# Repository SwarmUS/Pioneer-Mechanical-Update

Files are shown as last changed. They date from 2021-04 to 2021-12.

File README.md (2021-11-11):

# Pioneer-Mechanical-Update

This repository contains the 3D model of a modified Pioneer 2-DX used by the SwarmUS project.

## Requirements
- Solidworks 2021

## Getting started

This repository contains submodule of 3D model parts. Right after cloning the project and prior to opening any assembly, run the following command:

```
git submodule update --init --recursive
```

### Repository structure

------

```
Pioneer-Mechanical-Update
├── outputs
│   ├── dxf
|   ├── pdf
│   └── STL
|   	├── external
│   	└── internal
├── external
│   └── HiveBoard-BeeBoard-Mechanical
├── internal
├── Pioneer_originalRobotBase
├── pioneer2DX.SLDASM
└── README.md
```

#### pioneer2DX.SLDASM

Main assembly of the modified pioneer. It's composed of a Pioneer 3Dx chassis (which is the same as the Pioneer 2Dx) get from *Pioneer_originalRobotBase*, of components that are external to the robot (*external*) and of components that are internal to the robot (*internal*).

In this assembly, the Realsense D435i and its support are used but an additional models were made to use a D455 instead. The D455 version is include in assembly in hidden mode. 

Note: The wheels and the front sonar array are not included in the assembly since they are not useful to the sensors and electronics layouts. 

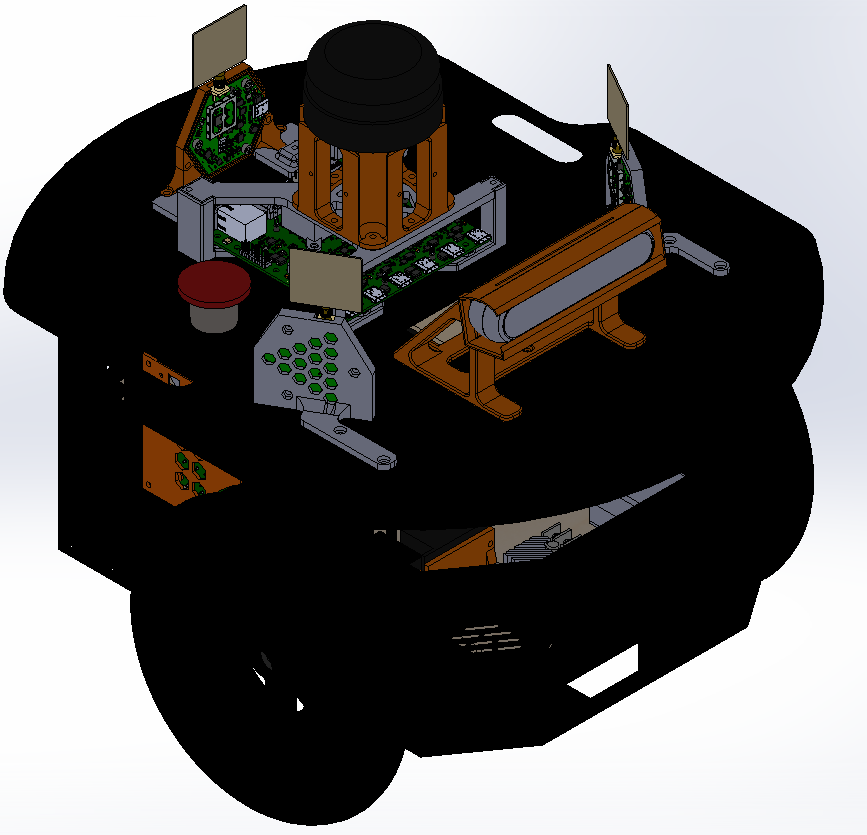
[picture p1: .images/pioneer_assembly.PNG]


### external

Contains the 3D models of the external components and their supports

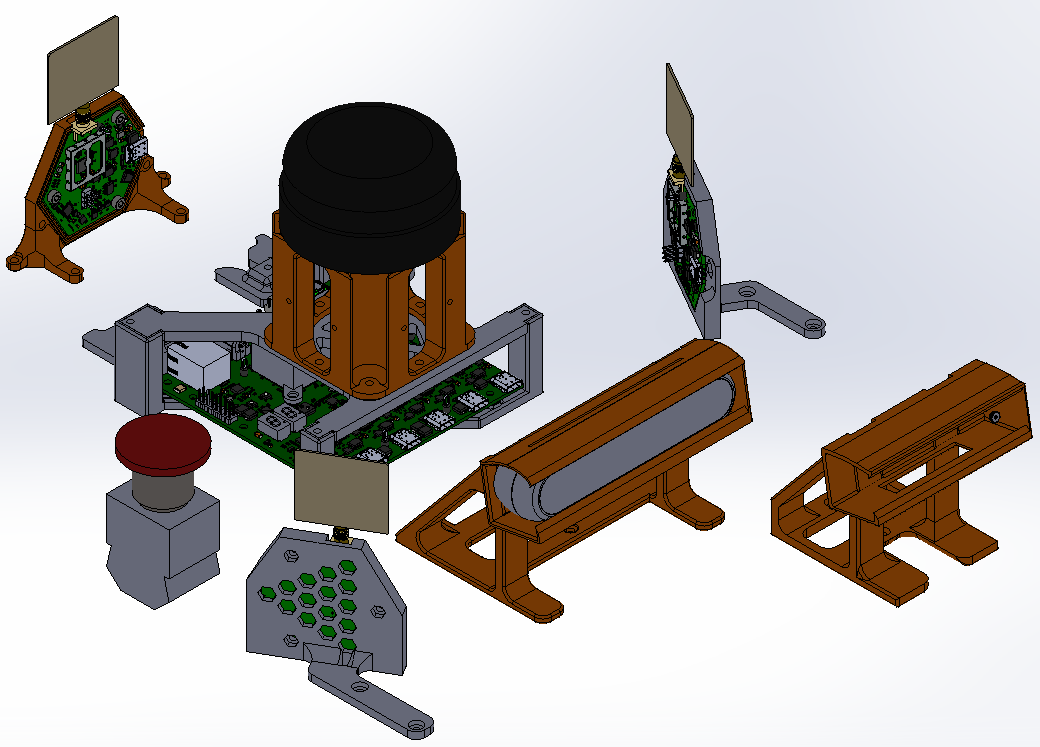
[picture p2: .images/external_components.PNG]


- **D435i**
  - **D435i_case.sldprt**: Realsense D435i protective case
  - **Intel_RealSense_Depth_Camera_D435.SLDASM**: 3D model of the camera distributed by Realsense [CAD Files (intelrealsense.com)](https://dev.intelrealsense.com/docs/cad-files)
  - **D435i_support.sldprt**: Camera stand that fits on the bolt pattern of the pioneer's top plate. The protective case is compatible with the support.
  - **D435i.SLDASM**: Assembly of the camera, its protective case and its support.
  - **protected_D435i.SLDASM**: Assembly of the camera and its protective case.
  
- **D455**
  
  - **D455_case.sldprt**: Realsense D455 protective case
  - **Intel_RealSense_D455_CAD_external_v2.SLDASM**: 3D model of the camera distributed by Realsense [CAD Files (intelrealsense.com)](https://dev.intelrealsense.com/docs/cad-files)
  - **D455_support.sldprt**: Camera stand that fits on the bolt pattern of the pioneer's top plate. The protective case is compatible with the support.
  - **D455_assembly.SLDASM**: Assembly of the camera, its protective  case and its support.
  - **protected_D455.SLDASM**: Assembly of the camera and its protective case.
  
- **motor_stop.SLDPRT**
  
  - Cad of the mushroom button used to disconnect the motor's power. Is mounted in a 22mm hole on the Pioneer's top plate.
  
- **Lidar**
  
  - **rplidar_simplified.SLDPRT**: 3D model of a simplified Rplidar A2M8.
- **lidar_support_april_tags.SLDPRT**: Lidar stand. We reused the already present bolt partern on the top plate of our Pionneer 2Dx to save time. The sides were designed to install a plate or sheet with AprilTags on them.
  
- **top_plate_modifications.SLDDRW**: Drawings of the additional holes that needs to be drilled on the Pioneer's top plate. One hole is for the mushroom button and the other one is an M3X0.5 tapped hole for the camera support. 

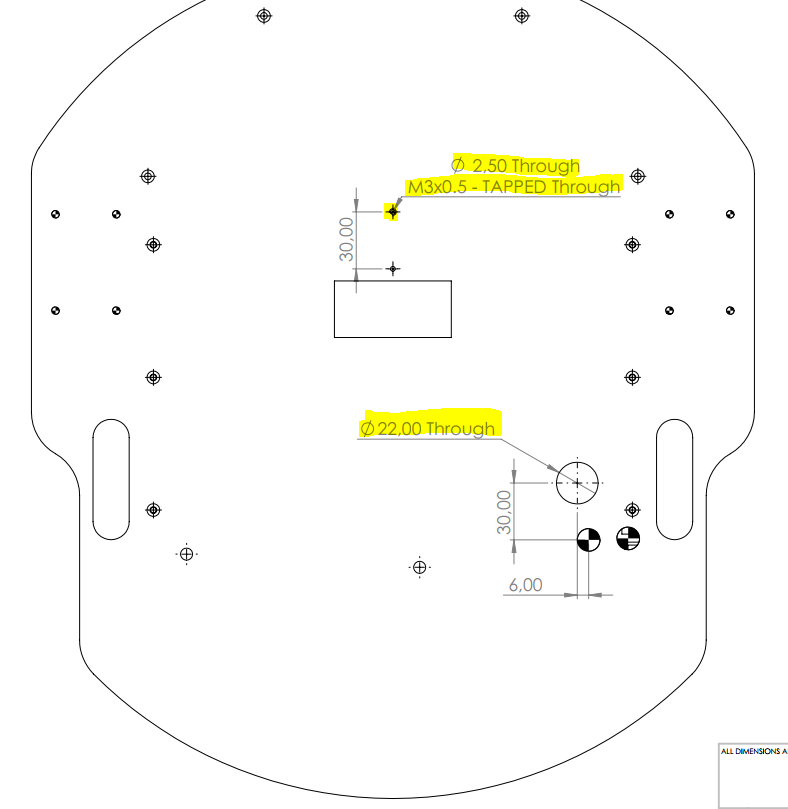
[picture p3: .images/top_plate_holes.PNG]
  

- **Board supports**
  - **HiveBoard-BeeBoard-Mechanical**: Submodule that contains the 3D model of the HiveBoard and BeeBoard PCBs and their default cases.
    - **HB_Plate.SLDPRT**: support the Hiveboard under the lidar.
    - **pioneer_bbmount_droit.SLDPRT**: supports the beeboard on the right side of the pioneer.
    - **pioneer_bbmount_gauche.SLDPRT**: supports the beeboard on the left side of the pioneer.  
    - **Lidar_support_over_HB.SLDPRT** support for lidarover the Hiveboard. All holes are for M3 screws and nuts.

### internal

Contains the 3D models of the internal components, their supports and big support plate.

- **Battery**

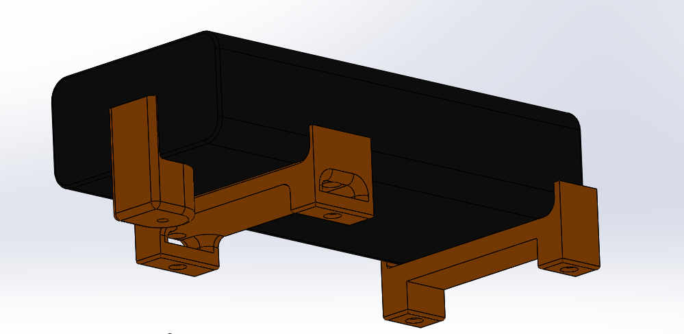
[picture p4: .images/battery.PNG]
  

  - **GOOLOO.SLDPRT**: Model of the battery. It's placed at the back of the robot since its the most accessible place to remove it and recharge it. 
  - **battery_holder_center.SLDPRT** , **battery_holder_side.SLDPRT** and **battery_stopper**: supports fixed on the internal plate. The battery sits in the supports to block its motion. An additional velcro strip can be installed in the middle support to strap the battery thus preventing it from moving up and down.

- **Support plate**

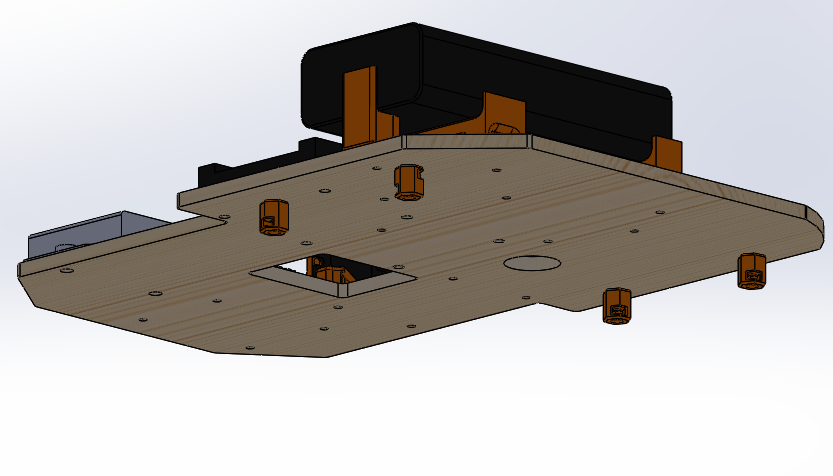
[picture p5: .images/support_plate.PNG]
  

  - **internal_support_plate_hole.SLDPRT** : Laser cut plate used to screw the components in place.
  - **small_plate_support.SLDPRT**: Small stands used to support the plate near the back of the robot. There are 4 of them and they are screwed on the bolt pattern of the bottom plate of the robot's chassis.
  
- **internal_electronics_plate.SLDASM**: Assembly of the circuits components and the support plate.

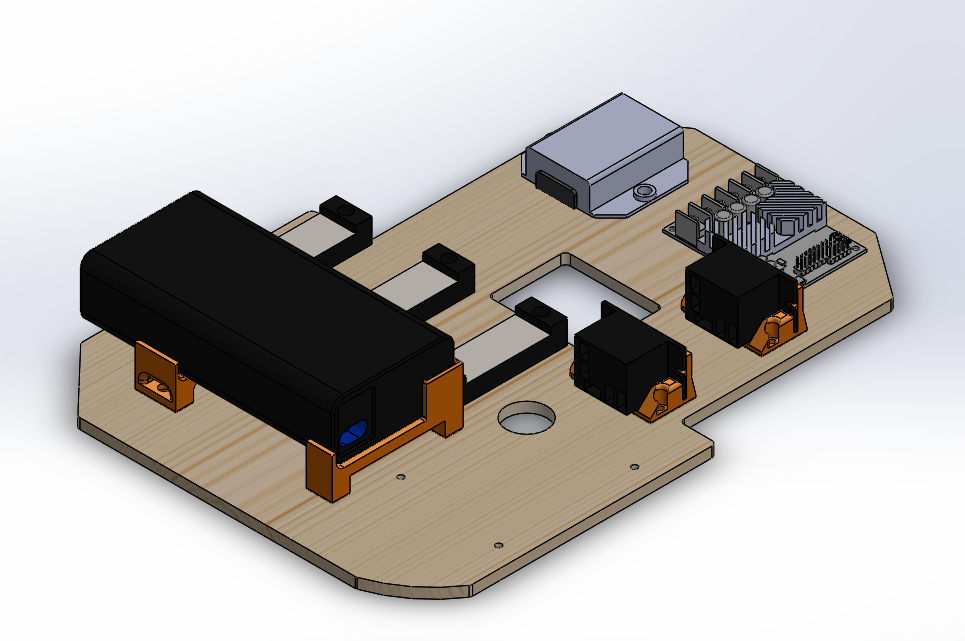
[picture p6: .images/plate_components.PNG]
  

  - **bornier.SLDPRT**: Screw terminals block.
  - **REG_313080006.SLDPRT**: 313080006 5V regulator
  - **Relays**
    - **relay.SLDPRT**: Relay
    - **relay_bracket.SLDPRT**: Bracket to hold the relay at a 90 degrees angle. This help with the electrical harness.
    - **relay_assembly.SLDASM**: Assembly of the relay and its bracket
  - **roboclaw_2X30A.SLDASM**: Motor controller CAD. Available at : [RoboClaw 2x30A Motor Controller (basicmicro.com)](https://www.basicmicro.com/RoboClaw-2x30A-Motor-Controller_p_9.html)

- **Computer's side pannel**

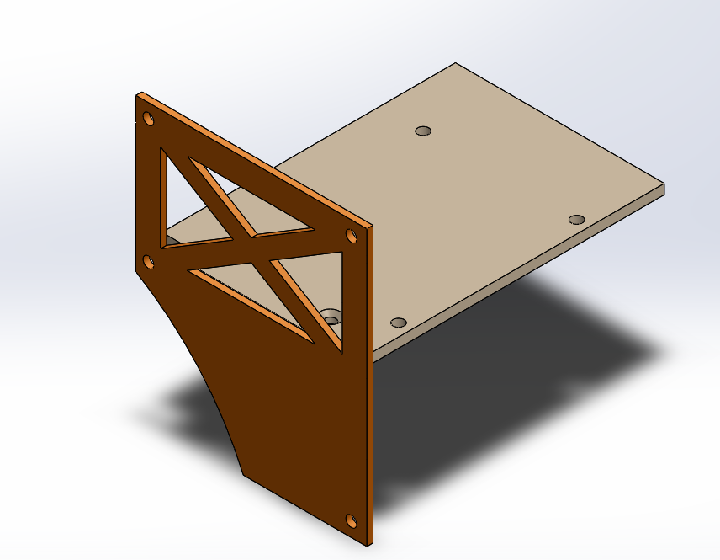
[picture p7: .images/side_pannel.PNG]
  

  - **computer.SLDPRT**: Box that represents the footprint of  Raspberry Pi 4 and a Jetson Nano ( sizes of their longest side with height of a Jetson). The CAD of the Raspberry Pi 4 is very heavy to load so this box is used as a lighter representation.

  - **side_pannel.SLDPRT**: Model of a panel that can be installed on the left-side slot of the pioneer to support a small plate. In our case, we used is to support the computer.

  - **computer_support.SLDPRT**: Plate that can be screwed on the *side_pannel.SLDPRT* . It has the bolt pattern to install a Rasberry Pi 4 or a Jeston Nano.

  - **computer_support_pi.SLDPRT**: Plate that can be screwed on the *side_pannel.SLDPRT* . It has the bolt pattern to install a Rasberry Pi 4. Was designed to have a more compact plate the selected computer is the Raspberry Pi 4. 

  - **supported_pi.SLDASM**: Assembly of the side pannel and the Raspberry Pi 4 support plate.

  - **fan_support.SLDPRT**: Support for the 5V fan that comes with the [LABIST Raspberry Pi 4 case]([LABISTS Case for Raspberry Pi 4](https://labists.com/products/raspberry-pi-4-case-kit)). Uses the screws provided with the kit.

  - **fan_support_m3.SLDPRT**: Support for the 5V [CANAKIT Pi fan](https://www.canakit.com/raspberry-pi-fan.html). Screwed with M3 fasteners.

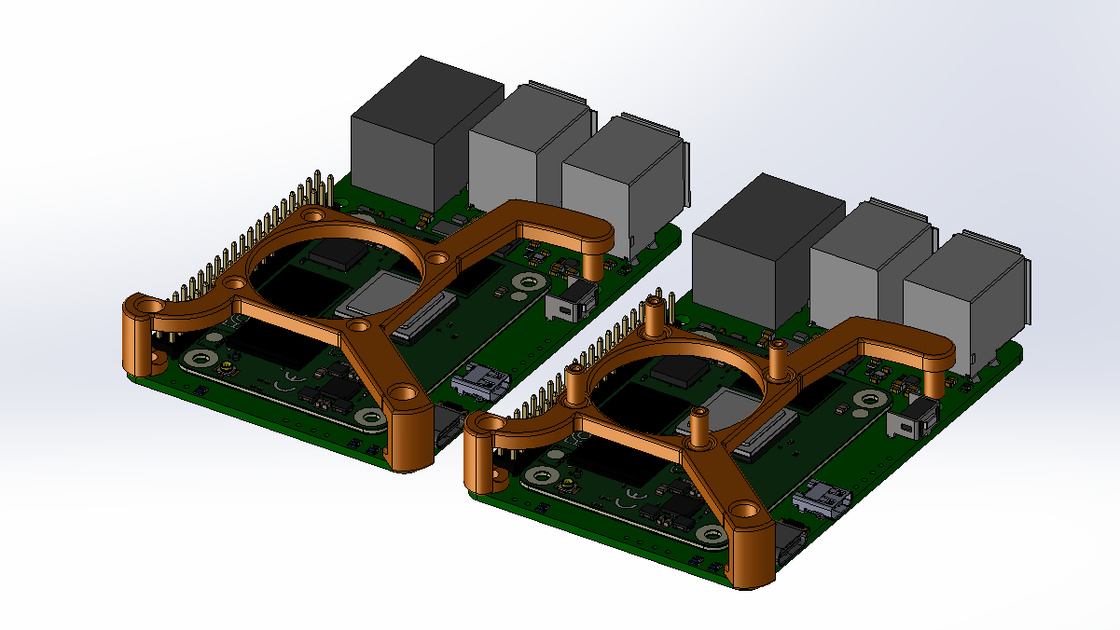
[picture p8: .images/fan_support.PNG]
    

  **Under Voltage Lock Out's (UVLO) side pannel**

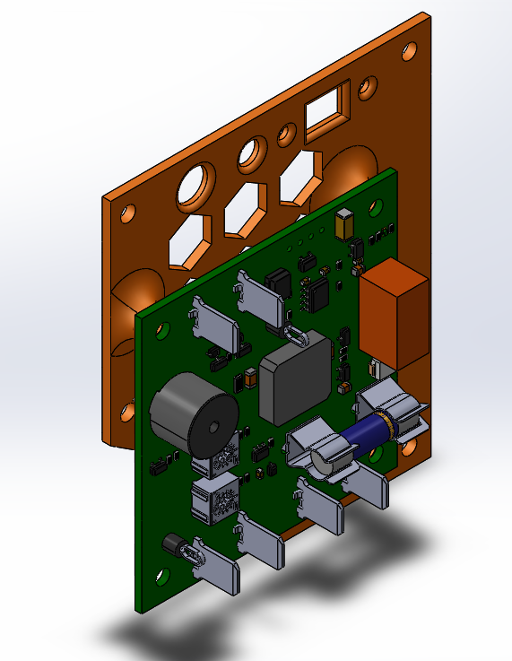
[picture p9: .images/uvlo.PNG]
  

  - **UVLO_MODULE_PCB REV Project_PCB_Rev.SLDASM**: CAD of the Under Voltage Lock Out module made by the SwarmUS electrical team. Used to disconnect the battery whenever it is below the selected voltage threshold. [Link]([Electrical/04 - UVLO_MODULE at master · SwarmUS/Electrical (github.com)](https://github.com/SwarmUS/Electrical/tree/master/04 - UVLO_MODULE)) to project.
  - **side_pannel_uvlo.SLDPRT**: Model of a panel that can be installed on the right-side slot of the pioneer to the UVLO printed circuit board with M3 screws . Used to support the UVLO printed circuit board and to have a placeholders for the starting pushbutton, the main power switch and a LED.
  - **supported_uvlo.SLDASM**: Assembly of the side pannel and the UVLO.

### **Pioneer_originalRobotBase**: 

Pioneer 3DX model that I took from:

[MathWorks Robotics and Autonomous Systems Team (2021). Mobile Robot Simulation for Collision Avoidance with Simulink (https://www.mathworks.com/matlabcentral/fileexchange/47208-mobile-robot-simulation-for-collision-avoidance-with-simulink), MATLAB Central File Exchange. Retrieved February 18, 2021.](https://www.mathworks.com/matlabcentral/fileexchange/47208-mobile-robot-simulation-for-collision-avoidance-with-simulink)

I had to redraw the motors(*internal/GM9236S01.SLDPRT*) since the motors were misaligned with their mounting hole in the chassis. 

I only used the main part of the chassis since all the other components are not on our real Pioneer 2Dx.

### Outputs

- STL files of the custom made part in order to 3D print them.
- DXF files of the custom 2D plate. A .swg and a .pdf was generated for each .dxf files with 0.001" paths with the colorRGB(255, 0, 0) . This can be used with a laser cutting machine.
- PDF files of the Pioneer top plate modification's drawing and the main assembly drawings. It indicates the position of the M3x0.5 tapped hole that needs to be added for the camera support and the position and the size of the mounting hole for the mushroom button.

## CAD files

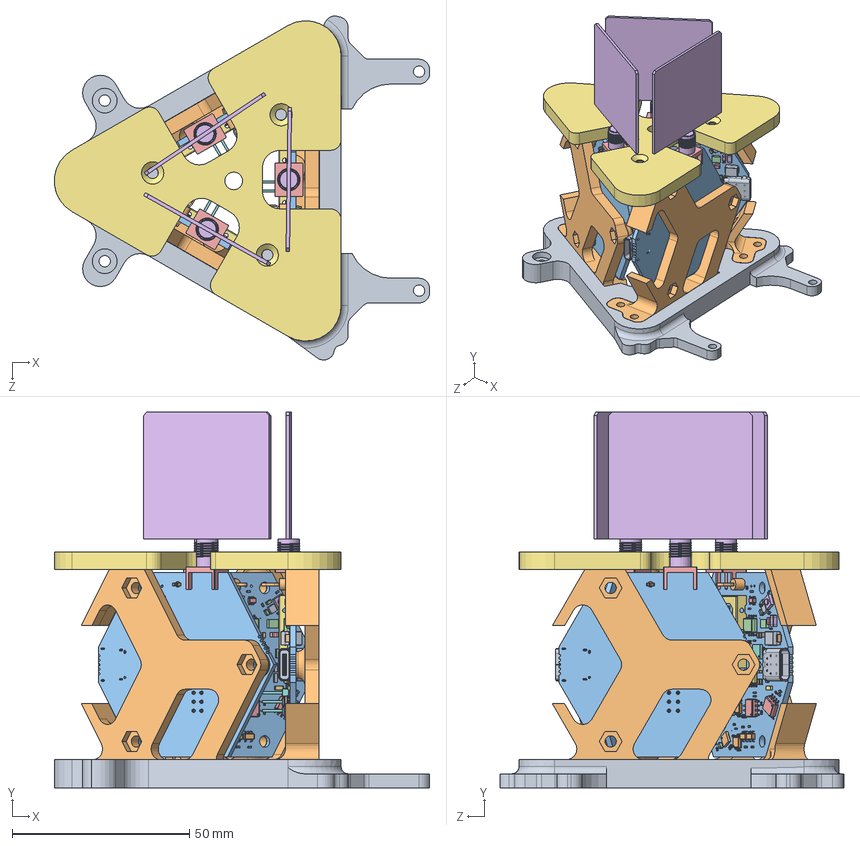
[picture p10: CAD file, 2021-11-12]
Antenna_puck/puck_assembly.SLDASM
105.9 x 106.1 x 97.0 mm
Triangle
Mount x 3
Open_CASCADE_STEP_translator_6.8_14.1-BB x 3
Open_CASCADE_STEP_translator_6.8_14.2.1-BB x 3
Leader-BB x 24
User_Library-User_Library-RES0402-2-BB x 123
Open_CASCADE_STEP_translator_6.8_10.1-BB x 3
Open_CASCADE_STEP_translator_6.8_10.2.1-BB x 3
Thermal_Shape-BB x 3
Open_CASCADE_STEP_translator_6.8_10.4.1-BB x 18
Extruded-BB x 3
Open_CASCADE_STEP_translator_6.8_1.1-BB x 3
Open_CASCADE_STEP_translator_6.8_1.2.1-BB x 3
Leader_2-BB x 24
74LVC1G386GW,125-BB x 3
Open_CASCADE_STEP_translator_6.8_1.1_2-BB x 3
Open_CASCADE_STEP_translator_6.8_1.2.1_2-BB x 3
Thermal_Shape_2-BB x 3
Open_CASCADE_STEP_translator_6.8_1.4.1-BB x 48
Open_CASCADE_STEP_translator_6.8_8.1.1-BB x 3
Leader_3-BB x 18
Open_CASCADE_STEP_translator_6.8_22.1-BB x 3
Open_CASCADE_STEP_translator_6.8_22.2.1-BB x 3
Thermal_Shape_3-BB x 3
Open_CASCADE_STEP_translator_6.8_22.4.1-BB x 48
Open_CASCADE_STEP_translator_6.8_14.1_2-BB x 3
Open_CASCADE_STEP_translator_6.8_14.2.1_2-BB x 3
Leader_4-BB x 24
Open_CASCADE_STEP_translator_6.8_1.1_3-BB x 3
Open_CASCADE_STEP_translator_6.8_1.2.1_3-BB x 3
Leader_5-BB x 24
Open_CASCADE_STEP_translator_6.8_11.1-BB x 6
Open_CASCADE_STEP_translator_6.8_11.2.1-BB x 6
Leader_6-BB x 60
Open_CASCADE_STEP_translator_6.8_14.1_3-BB x 3
Open_CASCADE_STEP_translator_6.8_14.2.1_3-BB x 3
Leader_7-BB x 24
Open_CASCADE_STEP_translator_6.8_20.1-BB x 3
Open_CASCADE_STEP_translator_6.8_20.2.1-BB x 3
Leader_8-BB x 42
Open_CASCADE_STEP_translator_6.8_4.1.1-BB x 6
Leader_9-BB x 30
Extruded_2-BB x 3
Extruded_3-BB x 24
WS-TASV_SMT_Tact_Switch_v4-BB x 3
RES0603-BB x 12
s10129381-X06002XLF-BB x 3
12401598E4#2A--3DModel-STEP-56544-BB x 3
keystone-PN5011-BB x 3
Pocket002-BB x 18
Pad004-BB x 18
Fillet-BB x 18
Pocket001-BB x 18
Pad-BB x 18
Open_CASCADE_STEP_translator_6.8_9.1-BB x 6
Open_CASCADE_STEP_translator_6.8_9.2.1-BB x 6
Open_CASCADE_STEP_translator_6.8_9.3.1-BB x 60
Open_CASCADE_STEP_translator_6.8_9.1_2-BB x 3
Open_CASCADE_STEP_translator_6.8_9.2.1_2-BB x 3
Open_CASCADE_STEP_translator_6.8_9.3.1_2-BB x 30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

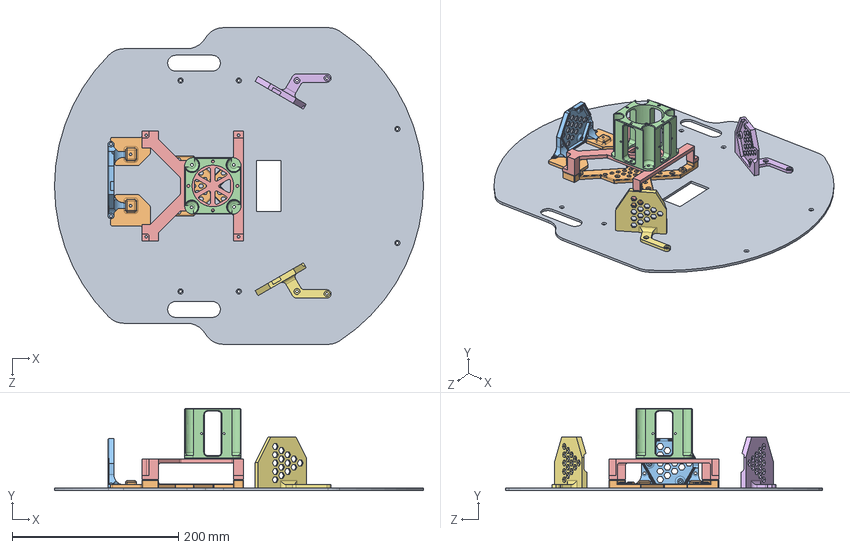
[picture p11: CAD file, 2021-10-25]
Top_plate_pionner (2021)/Assembly_complete.SLDASM
443.8 x 99.1 x 381.0 mm
Top_plate
plate_hb
bee_board_base_case
lidar_support_april_tags
top_HB
pionneer_bbmount_gauche_2
pionneer_bbmount_droit_2

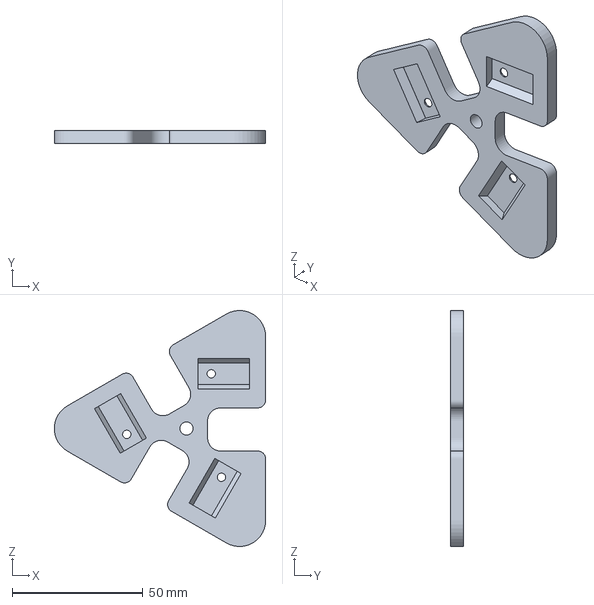
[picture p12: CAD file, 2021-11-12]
Antenna_puck/3MF/top_hat.3MF
80.9 x 5.00 x 90.3 mm

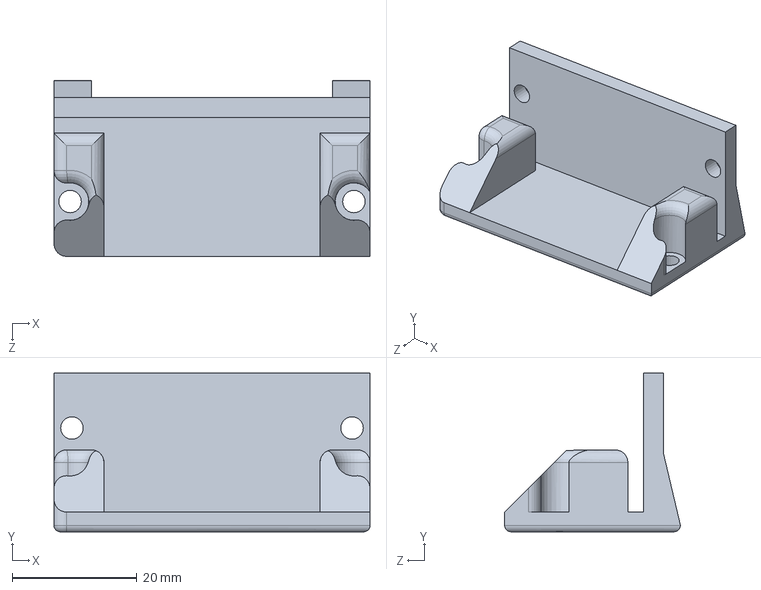
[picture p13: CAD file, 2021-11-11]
internal/relay_bracket.SLDPRT
50.6 x 25.4 x 28.1 mm

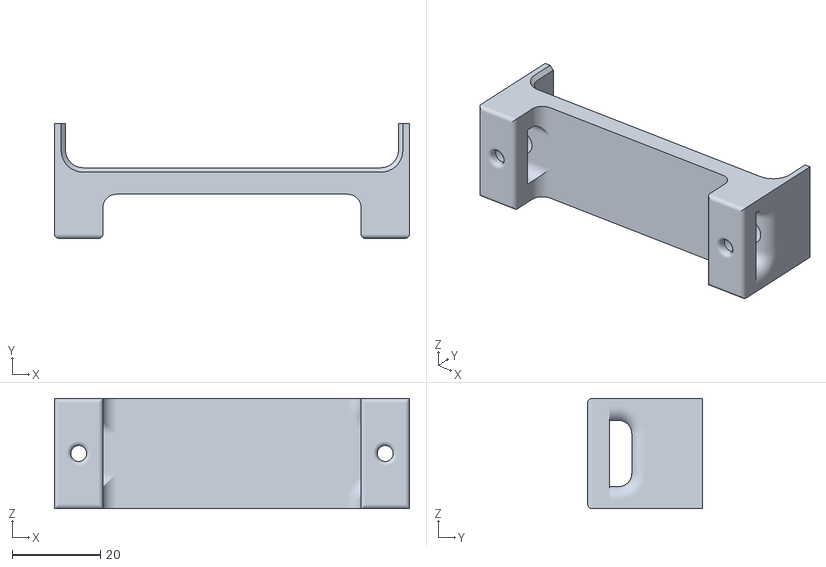
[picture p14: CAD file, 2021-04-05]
outputs/STL/internal/battery_holder_center.STL
80.5 x 26.0 x 25.0

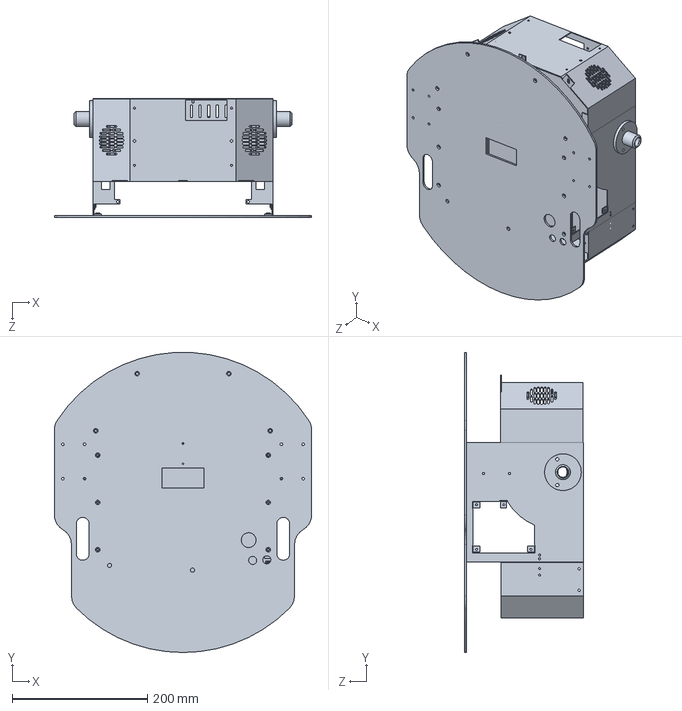
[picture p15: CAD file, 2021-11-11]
Pioneer_originalRobotBase/PioneerBody.SLDPRT
381.0 x 444.1 x 175.9 mm

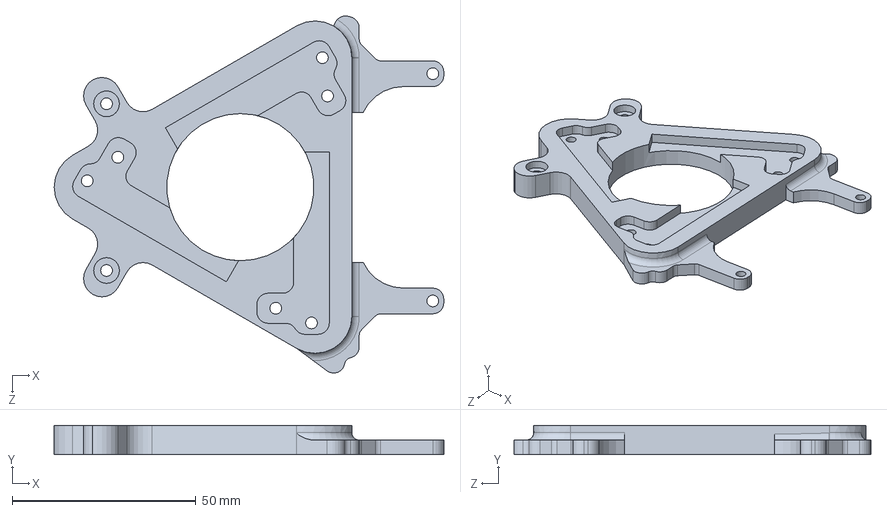
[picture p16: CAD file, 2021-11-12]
Antenna_puck/Triangle.SLDPRT
105.9 x 8.00 x 97.0 mm

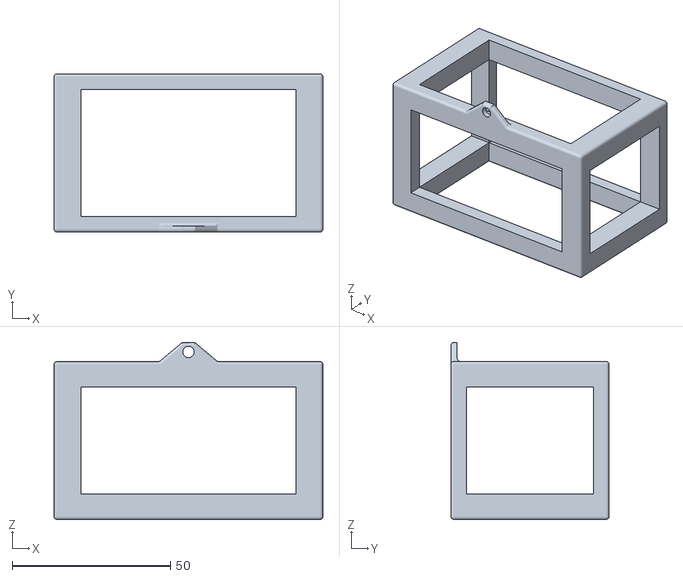
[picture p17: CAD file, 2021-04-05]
outputs/STL/internal/big_plate_support.STL
85.0 x 50.0 x 56.0

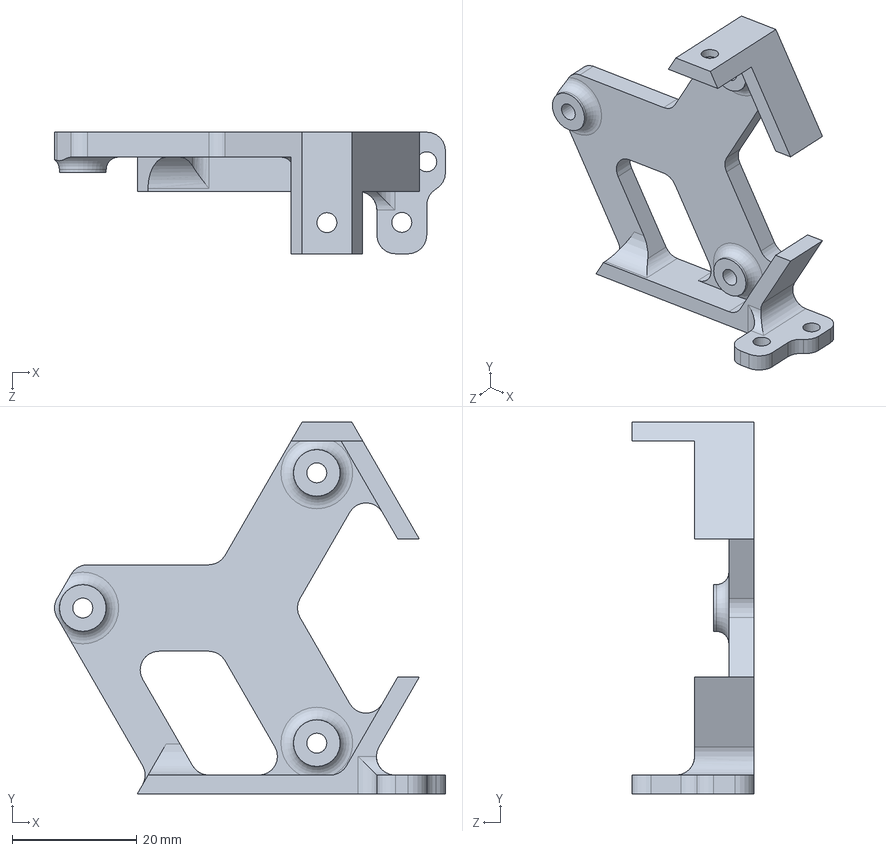
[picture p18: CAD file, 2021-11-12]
Antenna_puck/Mount.SLDPRT
62.7 x 59.6 x 19.5 mm

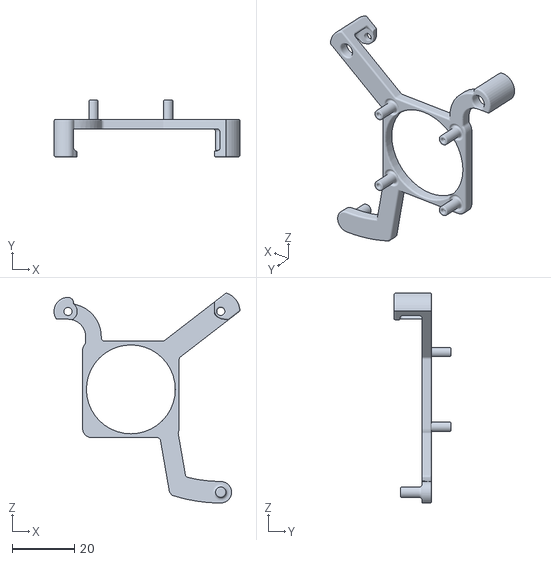
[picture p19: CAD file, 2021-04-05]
outputs/STL/internal/fan_support.STL
59.6 x 18.2 x 67.4

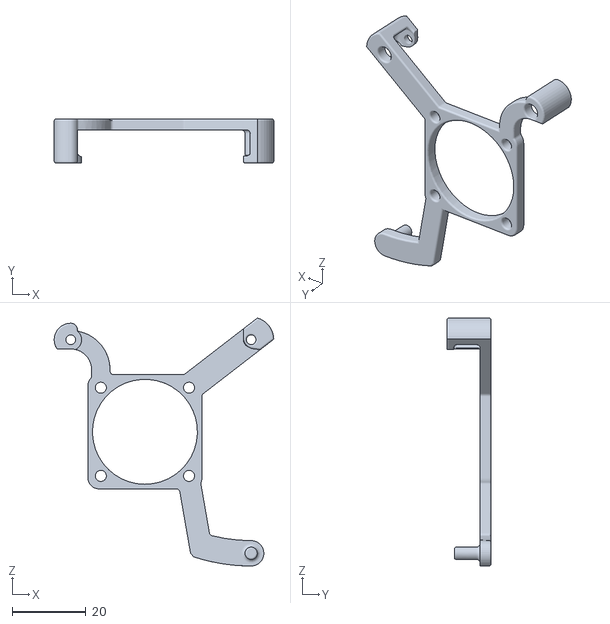
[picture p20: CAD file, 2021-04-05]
outputs/STL/internal/fan_support_m3.STL
59.6 x 12.0 x 67.4

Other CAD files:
internal/battery_holder_center.SLDPRT
Antenna_puck/3MF/Mount.3MF
Antenna_puck/3MF/Triangle.3MF
internal/90592A085_STEEL HEX NUT.SLDPRT
internal/GM9236S01.SLDPRT
internal/battery_stopper.SLDPRT
internal/computer.SLDPRT
internal/computer_support.SLDPRT
internal/fan_support.SLDPRT
internal/fan_support_m3.SLDPRT
internal/side_pannel.SLDPRT
internal/small_plate_support_nut.SLDASM

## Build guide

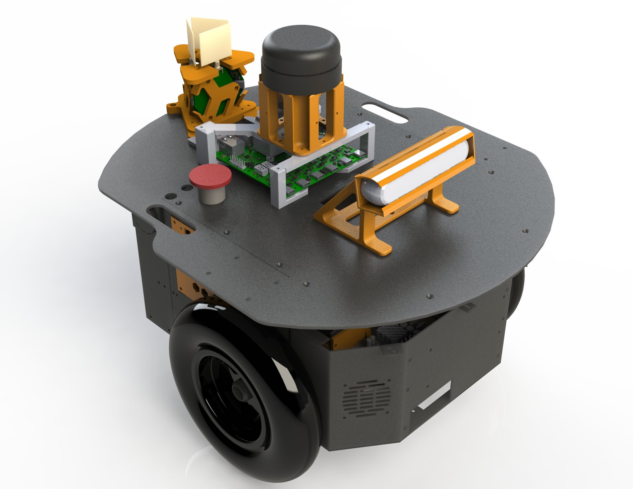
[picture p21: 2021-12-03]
.images/pioneer_assembly.png

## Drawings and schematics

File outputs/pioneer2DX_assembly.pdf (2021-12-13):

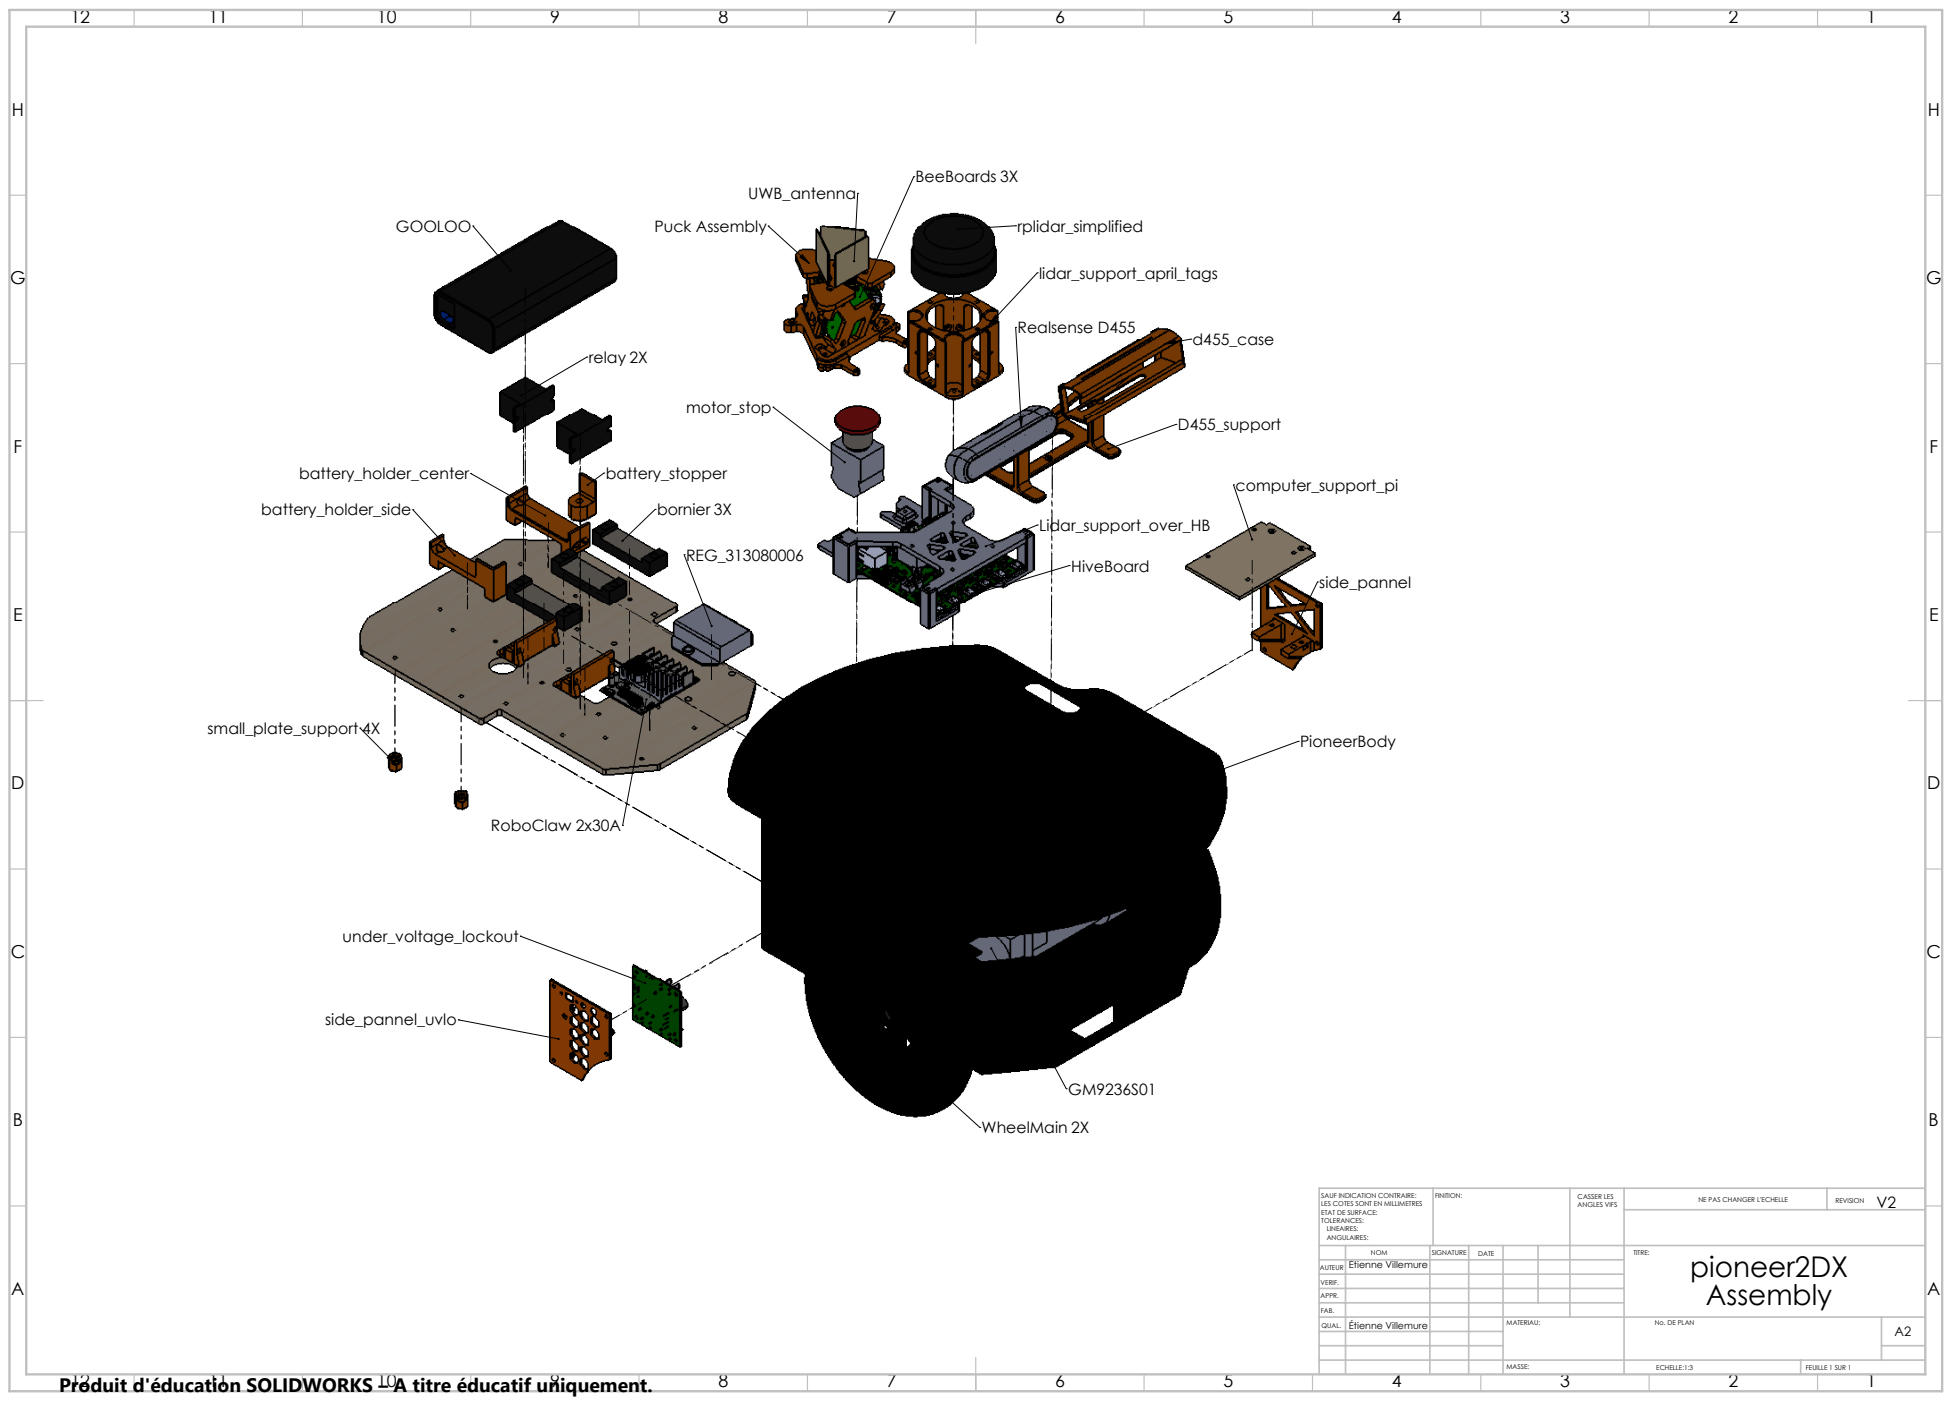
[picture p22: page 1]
relay 2X; small_plate_support 4X; bornier 3X; RoboClaw 2x30A; WheelMain 2X; Realsense D455; Puck Assembly; rplidar_simplified; BeeBoards 3X; ECHELLE:1:3; FEUILLE 1 SUR 1; Assembly A

SAUF INDICATION CONTRAIRE: LES COTES SONT EN MILLIMETRES ETAT DE SURFACE: TOLERANCES: LINEAIRES: ANGULAIRES: | FINITION: | CASSER LES ANGLES VIFS | NE PAS CHANGER L'ECHELLE | V2 REVISION

NOM | SIGNATURE | DATE | | | | TITRE: pioneer2DX

AUTEUR | Étienne Villemure

VERIF.
APPR.
FAB.
QUAL. | Étienne Villemure | | | MATERIAU: | No. DE PLAN | A2

Produit d'éducation SOLIDWORKS – A titre éducatif uniquement.

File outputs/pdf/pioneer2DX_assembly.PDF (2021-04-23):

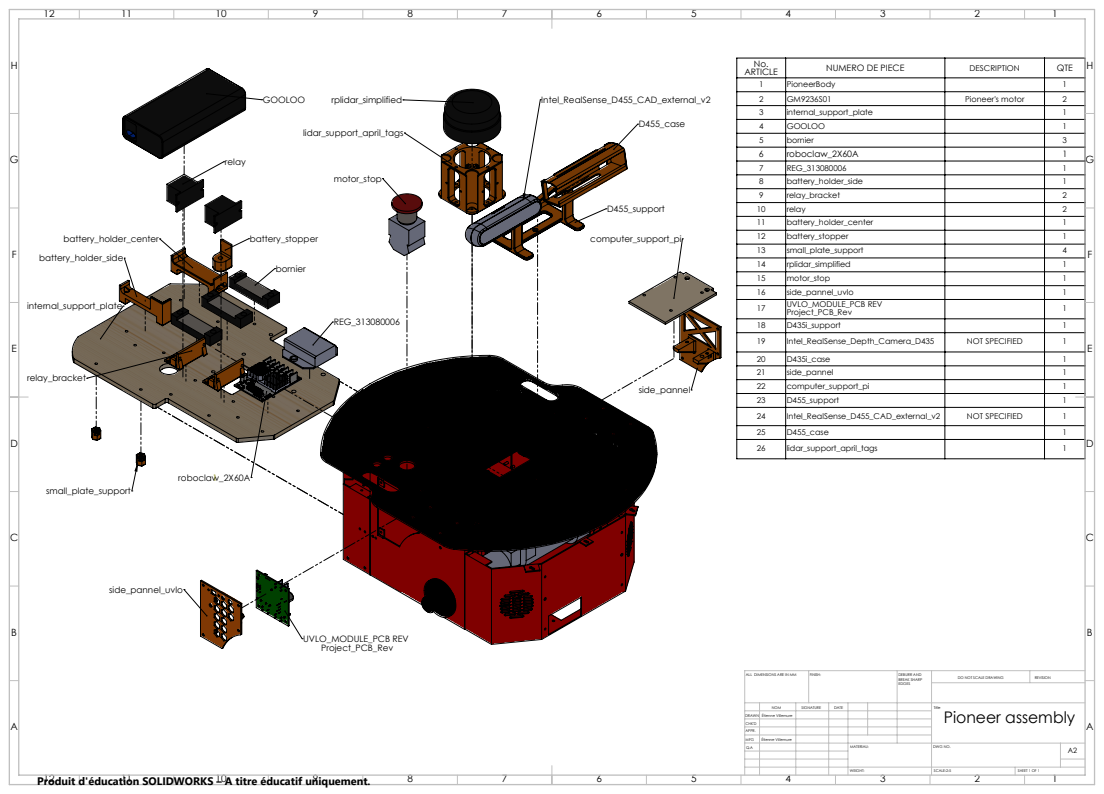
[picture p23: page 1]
roboclaw_2X60A 1; UVLO_MODULE_PCB REV; SCALE:2:5; SHEET 1 OF 1; Pioneer assembly A

No. ARTICLE | NUMERO DE PIECE | DESCRIPTION | QTE

1 | PioneerBody | | 1
2 | GM9236S01 | Pioneer's motor | 2
3 | internal_support_plate | | 1
4 | GOOLOO | | 1
5 | bornier | | 3
6 | roboclaw_2X60A | | 1
7 | REG_313080006 | | 1
8 | battery_holder_side | | 1
9 | relay_bracket | | 2
10 | relay | | 2
11 | battery_holder_center | | 1
12 | battery_stopper | | 1
13 | small_plate_support | | 4
14 | rplidar_simplified | | 1
15 | motor_stop | | 1
16 | side_pannel_uvlo | | 1
17 | UVLO_MODULE_PCB REV Project_PCB_Rev | | 1
18 | D435i_support | | 1
19 | Intel_RealSense_Depth_Camera_D435 | NOT SPECIFIED | 1
20 | D435i_case | | 1
21 | side_pannel | | 1
22 | computer_support_pi | | 1
23 | D455_support | | 1
24 | Intel_RealSense_D455_CAD_external_v2 | NOT SPECIFIED | 1
25 | D455_case | | 1
26 | lidar_support_april_tags | | 1

ALL DIMENSIONS ARE IN MM | FINISH: | DEBURR AND BREAK SHARP EDGES | DO NOT SCALE DRAWING | REVISION

NOM | SIGNATURE | DATE | | | | Title

DRAWN | Étienne Villemure
CHK'D
APPR.
MFG | Étienne Villemure
Q.A | | | | MATERIAU: | DWG NO. | A2

Produit d'éducation SOLIDWORKS – A titre éducatif uniquement.

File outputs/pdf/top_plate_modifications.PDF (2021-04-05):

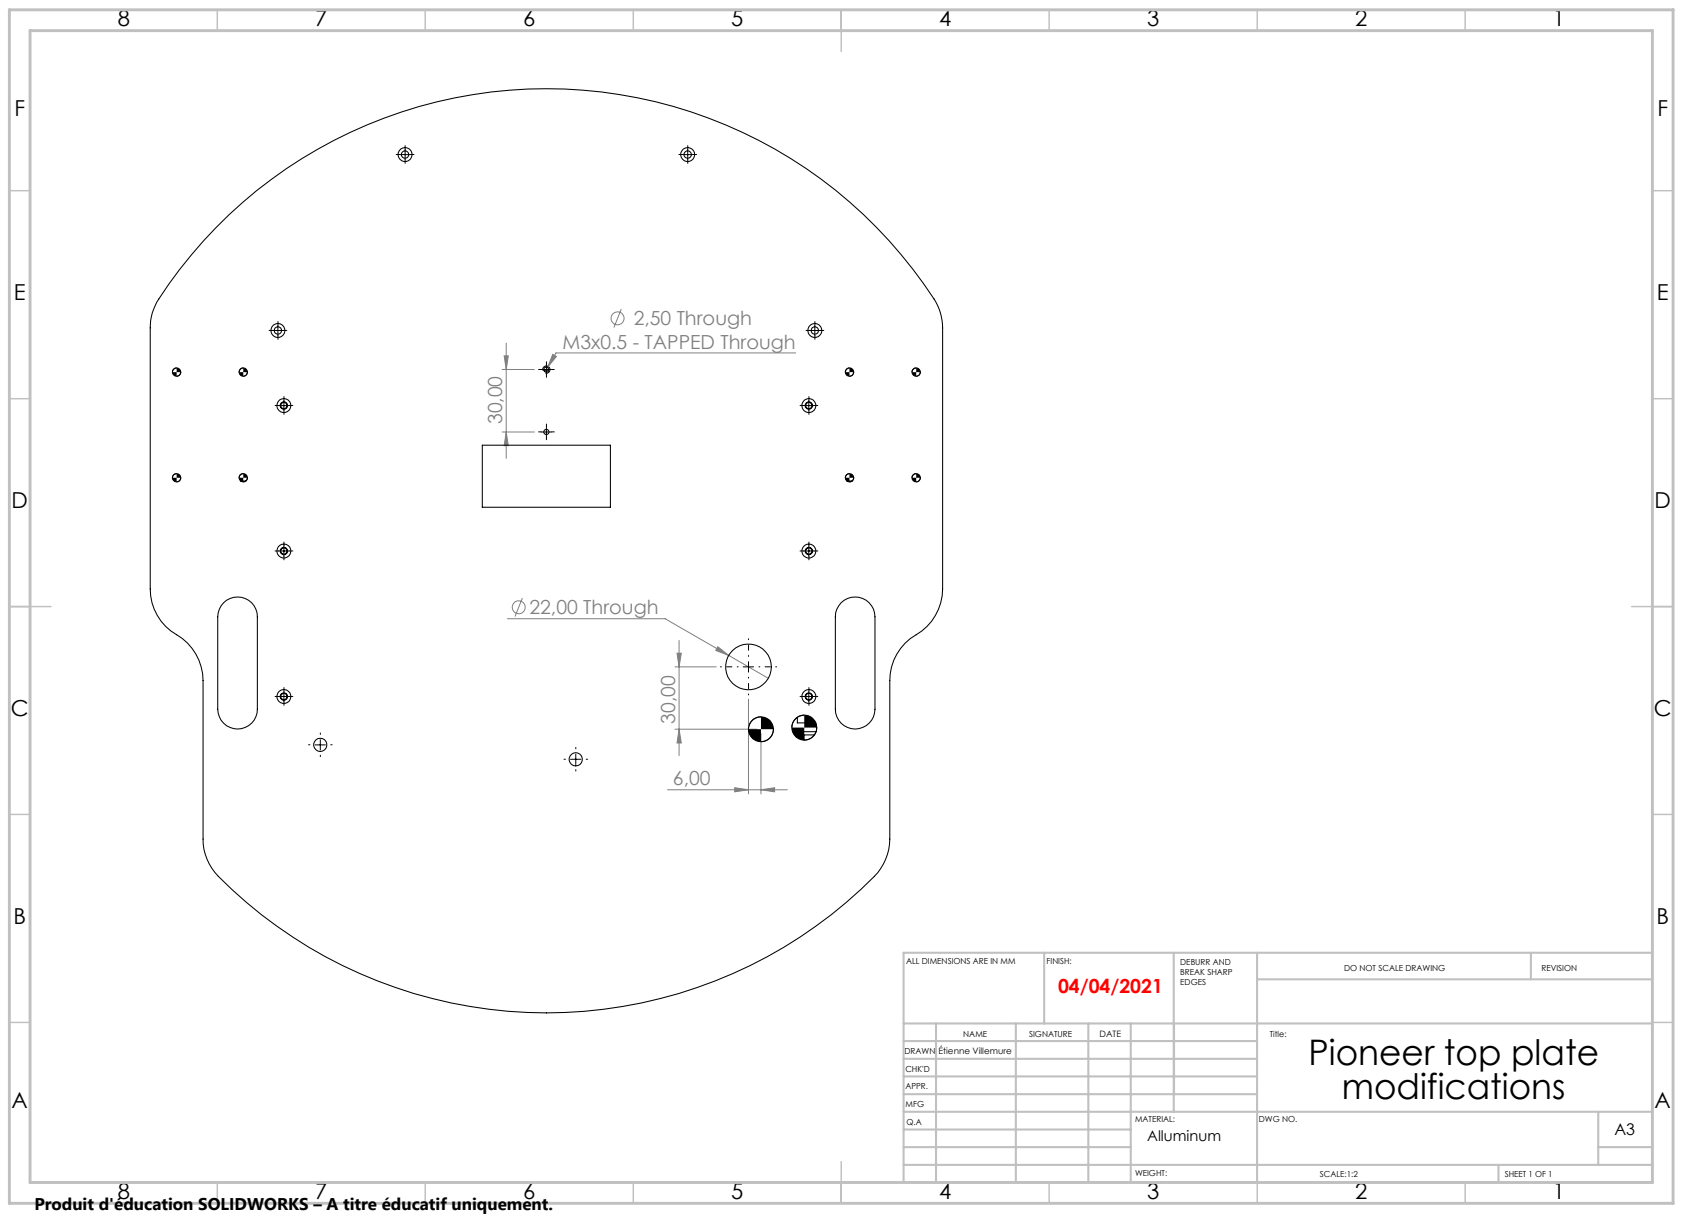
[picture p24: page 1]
22,00 Through; 2,50 Through M3x0.5 - TAPPED Through; ALL DIMENSIONS ARE IN MM; FINISH:; DEBURR AND; BREAK SHARP; DO NOT SCALE DRAWING; REVISION; SCALE:1:2; SHEET 1 OF 1; modifications A

NAME | SIGNATURE | DATE | | | Title: Pioneer top plate

DRAWN | Étienne Villemure
CHK'D
APPR.
MFG
Q.A | | | | MATERIAL: Alluminum | DWG NO. | A3

Produit d'éducation SOLIDWORKS – A titre éducatif uniquement.

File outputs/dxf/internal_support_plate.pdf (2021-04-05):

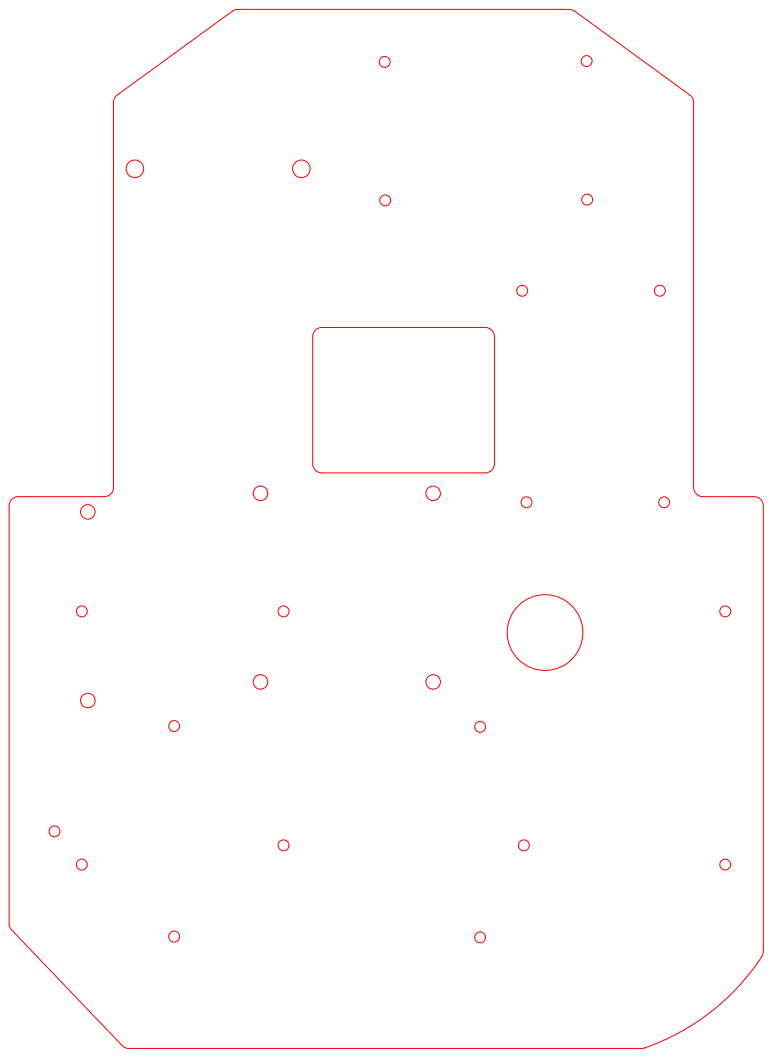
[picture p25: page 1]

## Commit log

2021-03-05 Remove Schottky diode
2021-03-05 Added a new lidar support design in order to install appril tag on it and regenerated STL files
    [lidar_support.STL]
2021-03-05 Added assemblies for the cameras, their case and their support. Adjusted the D455 case to fit better with its support. Regenerated STL files
2021-03-05 Added a fan holder for the raspberry pi 4
    [fan_support.SLDPRT, fan_support.STL]
2021-03-05 Added a bracket to hold the relays at 90 degres
    [relay_assembly.SLDASM, relay_bracket.SLDPRT, relay_bracket.STL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]
2021-03-05 Changed the internal component placement and the support plate
    [PioneerBody.SLDPRT, internal_suport_plate.DXF, internal_suport_plate.SLDPRT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]
2021-04-04 Cleanup initial commit
    [PioneerBody.SLDPRT, battery_holder_center_V2.SLDPRT, battery_holder_center_V2.STL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]
2021-04-04 Cleanup
    - Removed unused parts and assemblies
    - Changed the lidar support in Pioneer assembly
    [battery_holder_center.SLDPRT, big_plate_support.SLDASM, big_support_long_side_0P125.SLDPRT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]
2021-04-04 Removed outputs
    - Removed the output files since they will be regenerated
    [battery_holder_center.STL, battery_holder_center_V2.STL, battery_holder_side.STL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]
2021-04-04 Removed old lidar support
2021-04-04 Removed unused part
    [battery_holder_side_2.SLDPRT]
2021-04-04 Replaced part
    - Replaced the battery_holder_center_V2 to be the actual part used
    [battery_holder_center.SLDPRT, battery_holder_center_V2.SLDPRT]
2021-04-04 Generated STL files of internal components
    [battery_holder_center.STL, battery_holder_side.STL, battery_stopper.SLDPRT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]
2021-04-04 Generated DXF files of internal plates
    [big_plate_support.SLDPRT, computer_support.DXF, computer_support_pi.DXF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]
2021-04-04 Added drawing for top plate drilled holes
    [PioneerBody.SLDPRT]
2021-04-04 Added the tapped hole annotation
    [PioneerBody.SLDPRT]
2021-04-05 Modified fan supports
    - Renamed the fan support with the M3 screws
    - Add an orange color to the fan supports
    - Change the distance of the hole in the legs to match correctly the RPI4 bolt pattern
    [fan_support.SLDPRT, fan_support.STL, fan_support_m3.SLDPRT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]
2021-04-05 Update the main assembly
    [internal_support_plate.SLDPRT, relay_assembly.SLDASM, supported_pi.SLDASM]
2021-04-23 Removed unused parts
    [big_plate_support.SLDPRT, fan_support_m3_fan.STL]
2021-04-23 Changed assemblies' properties for BOM
    - Changed assemblies' properties so internal parts of PCBs are not displayed in drawing's BOM
    [PioneerBody.SLDPRT, roboclaw_2X30A.SLDASM, roboclaw_2X60A.SLDASM]
2021-04-23 Created small plate supports with their M3 nuts
    [small_plate_support_nut.SLDASM]
2021-04-23 Create assembly drawings
    - Added two explosed view configurations for the main assembly
    - Added a drawing of the explosed view
2021-04-28 Roboclaw model change
    - Finally the roboclaw is a 2x30A
    [roboclaw_2X30A.SLDASM, roboclaw_2X60A.SLDASM]
2021-10-07 test 2020 -> 2021
    [test_part.SLDPRT]
2021-10-14 update models
    [Assemblage1.SLDASM, Assemblage2.SLDASM, HIVE_BOARD.SLDPRT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]
2021-10-14 Push for 2021 version
    [Assemblage.SLDASM, Assemblage1.SLDASM, Assemblage2.SLDASM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]
2021-10-16 Modified Pioneer body
    - Added main wheels and caster wheel
    - Changed color of the wheels to black to reflect real life robot
    - Changed the color of the pioneer body to reflect real life color of the robot.
    [CasterWheelBody.SLDPRT, CasterWheelClamp.SLDPRT, GM9236S01.SLDPRT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]
2021-10-20 update plate_hb
    [HIVE_BOARD.SLDPRT, Top_plate.SLDPRT, plate_hb.SLDPRT]
2021-10-20 Upper plate update
    [Assemblage.SLDASM, plate_hb.SLDPRT, top_HB.SLDPRT]
2021-10-21 top plate reapperance
    [Top_plate.SLDPRT]
2021-10-21 Top_hb changé
    [Assemblage.SLDASM, Top_plate.SLDPRT, top_HB.SLDPRT]
2021-10-22 Removed test part
    [test_part.SLDPRT]
2021-10-23 Update for pionneer
    [Assembly_complete.SLDASM, HIVE_BOARD.step.SLDPRT, Top_plate.SLDPRT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]
2021-10-25 Assembly Pionneer final
    [Assemblage.SLDASM, Assembly_complete.SLDASM, Top_plate.SLDPRT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]
2021-10-26 hoping the last one
    [Top_plate.SLDPRT, bbmount_both.STL, pionneer_bbmount_droit.STL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]
2021-10-27 Added new parts for top - made change for base plate
    [pionneer_bbmount_droit_2.SLDPRT, pionneer_bbmount_gauche_2.SLDPRT, plate_hb.SLDPRT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]
2021-10-29 last update +3MF files
    [pionneer_bbmount_droit_2.3MF, pionneer_bbmount_gauche_2.3MF, plate_hb.3MF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]
2021-10-30 Cleanup before PR
    [Assemblage.SLDASM, CasterWheelBody.SLDPRT, CasterWheelClamp.SLDPRT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]
2021-10-31 Naming correction and README update
    - Fixed the typo of the BB mount since pioneer had 2 n (pionNeer)
    - Update README to add the submodule, update images and correct typo
2021-11-11 added antenna puck
    [Footprint + position de l'antenne.SLDPRT, Mount.SLDPRT, Triangle.SLDPRT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]
2021-11-11 triangle avec pattes
    [Triangle.SLDPRT]
2021-11-12 Last update before print
    [Mount.SLDPRT, Triangle.SLDPRT, Triangle_HB_Plate.SLDASM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]
2021-12-03 Updated BeeBoard puck
    - Bump the HB-BB-Mechanical to have access to the BeeBoard puck
    - Change the BeeBoard configuration for the BeeBoard puck
    - Changed the texture of the Pioneer's wheel to black
    - Remove pioneer's image from git cache
    [WheelMain.SLDPRT]
2021-12-13 Updated the exploded view
    [roboclaw_2X30A.SLDASM]
